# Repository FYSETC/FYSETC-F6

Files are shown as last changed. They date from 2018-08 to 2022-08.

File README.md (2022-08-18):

## Product Introduction

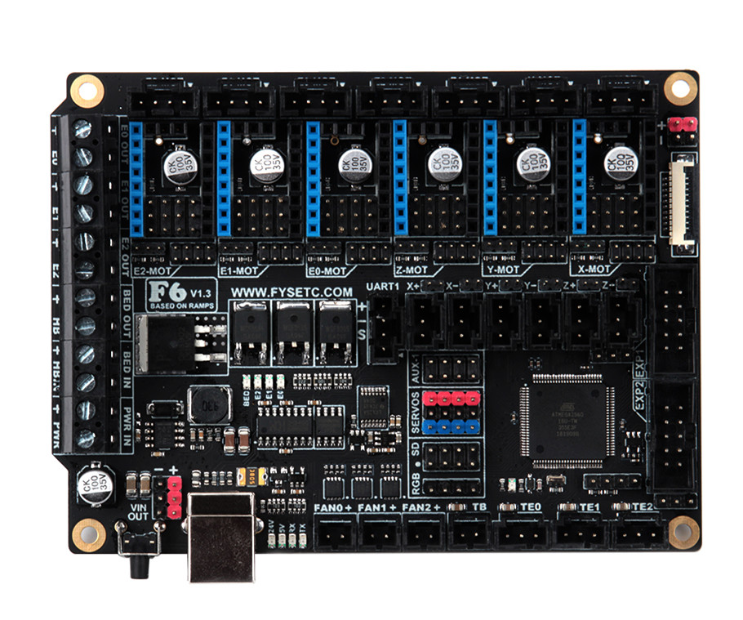
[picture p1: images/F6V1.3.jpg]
F6V1.3


The FYSETC F6 board is a feature rich all-in-one electronics solution for 3D printer and other CNC devices.  It provides six drivers slots and supports Pololu pin compatible stepper drivers, especially the TMC drivers modules. There is no need for flying wires when using TMC2100, TMC2130 and TMC2208. and SPI,Usart and ther pin configer functions are available.

## Features

- Compact size: 117mm x 87mm
- fully integrated all in one solution:
  - Arduino 2560-R3 compatible (works with Sprinter, Repetier-Firmware, Marlin out of the box)
  - CH340 for high speed USB serial connection 
- UNIVERSAL POWER:
  - can be used with 9V-28V for motors / heated bed
  - integrated high precision power regulators (DC/DC):  5V 3A Max 
  - power input auto selector for ATmega/logic (stand alone or power from USB)
- Easy DISPLAY + SD-CARD connector:
  - RepRapDiscount SmartController compatible pin header on board
  - **10P FPC for Serial Touch display**
  - 2X4 PinHeader Out for SD Card moudle 
- **Up to 6 motor drivers with easy micro-steps setup and Supports TMC driver without flying wire**
- 10x PWM capable power mosfet outputs (1 for HotBed, 3 for Heat-End, 3 for fans, 3 for RGB LED strip) 
- The Hot-Bed is designed as a separate power input for maximum current
- All unused pins are led out by pin headers
- <font color=#0099ff size=3 face="~~On Board External 2Mb SPI Flash~~">~~On Board External 2Mb SPI Flash~~</font> 
- PCB：
  - 4 layer
  - 2OZ copper inner layers，1OZ out layers
  - High quality, High temperature FR4-TG130 PCB
  - Gold ENIG finishing

## Application

- 3D printer 
- CNC Device
- Other similar machines

## Hardware Reasources

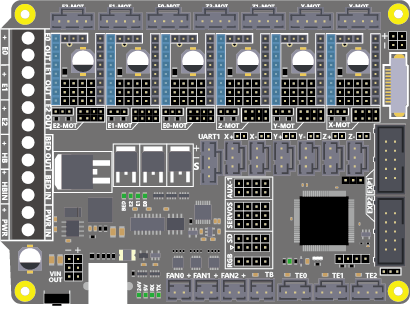
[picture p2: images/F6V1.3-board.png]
F6V1.3-board


| Board Name | F6 |
| --- | --- |
| License | GPL V2.0 |
| Latest Version | V1.3 |
| Extruders | 3 |
| Fixed Fans | 5 Max |
| Controlled Fans | 3 Max |
| Heaters | 3 Max |
| Endstops | 6 Max |
| Temp sens | 4 Max |
| SPI | 1 |
| I2C | 1 |
| ISP | 1 |
| Serial port chip | CH340 |
| CPU | Atmega2560 |
| CPU Speed ( MHz ) | 16 Mhz |
| Stepper driver | 6 Max |
| Stepper driver  Type | All StepStick compatible modules |
| Input | Main PWR：12-24V 10A Max；BED IN：12-24V 15A Max |
| Output | BED OUT：15A Max ；Heater Out：5A Max |

## Jumper for different drivers

In order to support as many different drivers as possible, F6 sets a lot of jumper positions. Different drive modules require different jumpers. The following is a detailed description:

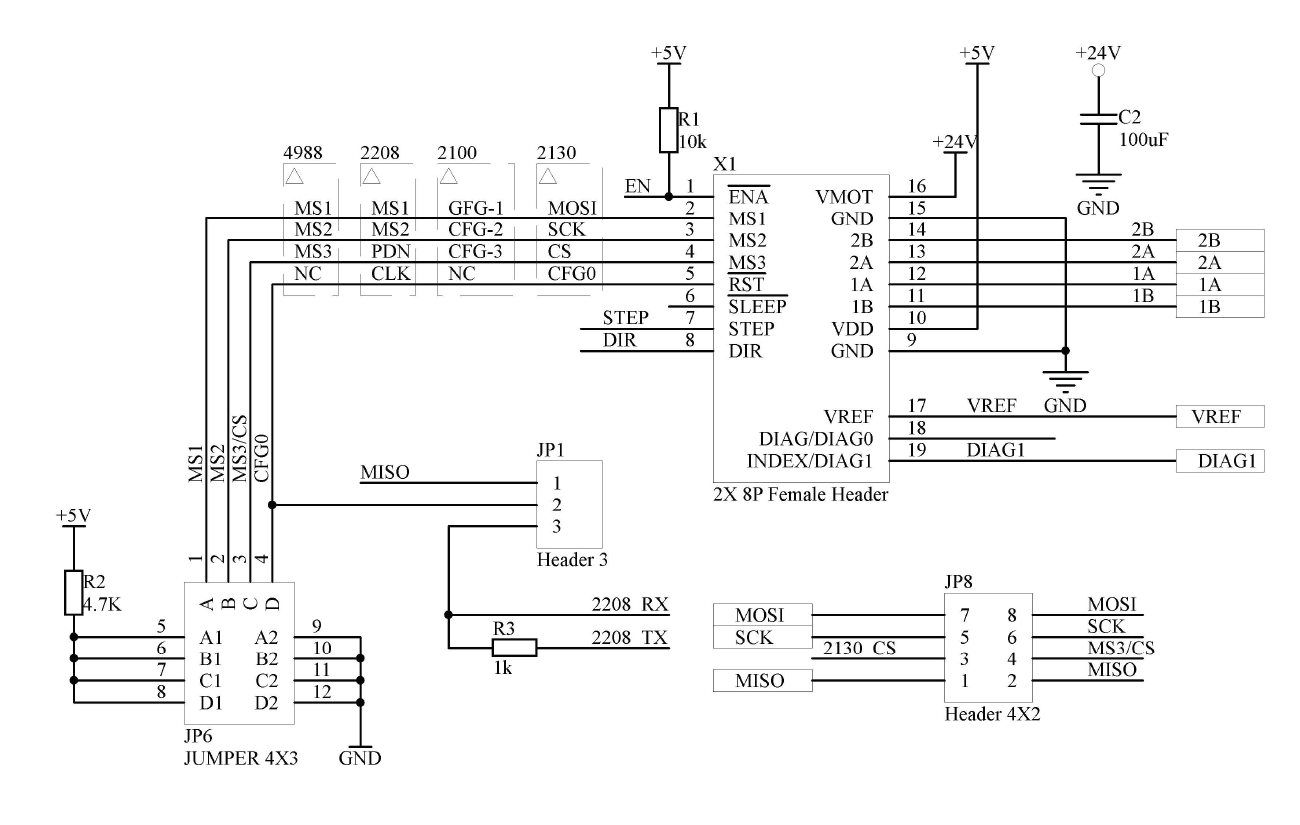
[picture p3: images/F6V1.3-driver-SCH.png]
F6V1.3-driver-SCH


As shown in the schematic diagram above, there are three sets of jumpers in the drive section: JP1, JP6, and JP8. The different driver correspondences are shown in the following table:

| Divers Class | Used jumpers |
|:---:|:---:|
| A4988/DRV8825/THB6128/LV8729 | JP6（only ABC ways） |
| TMC2100 | JP6（only AB ways） |
| TMC2208 | JP1（Short 2&3）&  JP6 |
| TMC2130 | JP1（Short 1&2）&  JP8（Short All） |

#### 1- A4988 and similar series

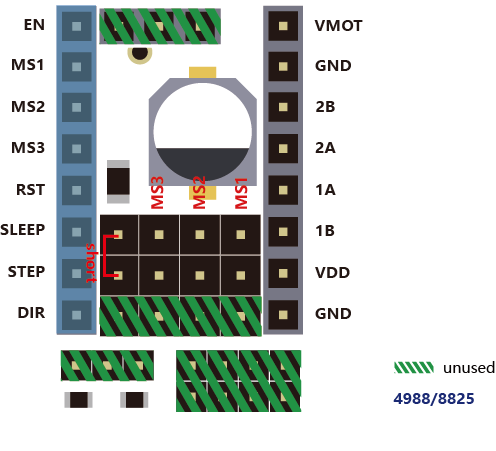
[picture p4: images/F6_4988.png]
F6_4988


If you use the normal A4988 series module, you only need to set the jumper according to the position shown in the figure above, and you should not insert any jumpers in the shaded green part.

#### 2-TMC2100

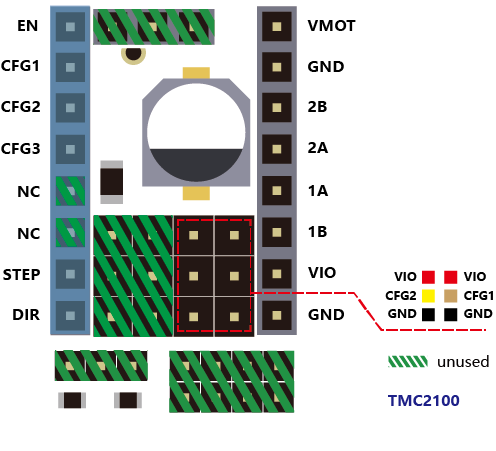
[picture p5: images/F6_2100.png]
F6_2100
 

If you use the TMC2100 module and want to change its microsteps and mode settings, first you must ensure that the CFG1 and CFG2 of the 2100 module are connected by a pin next to it. (For the FYSETC version, you can only perform the welding configuration on the board. The default CFG1 And CFG2 is not connected to the pin header, and the connected version will be sold later)

#### 3-TMC2208

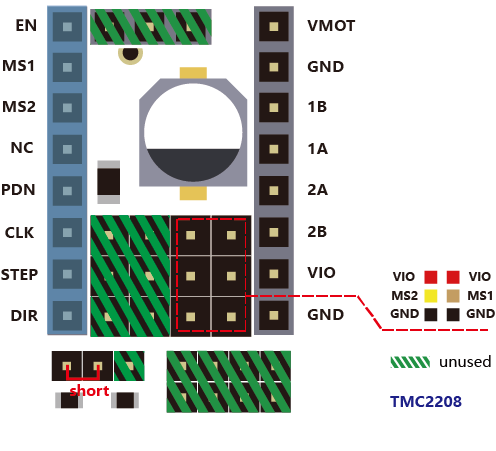
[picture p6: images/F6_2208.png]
F6_2208


If you use the TMC2208, there are two modes to choose . FYSETC's 2208 is factory defaulted to standalone mode. At this mode, you can only set the microsteps by MS1 and MS2.
If you want to config more , you need to enable PDN. First, You must make the jumper next to the PDN pin closed, and second, make sure that the 2 and 3 pin of the JP1 jumper next to the drive position on F6 board is connected , and then, you can make the configuration of the 2208 with marlin (SoftwareSerial).

#### 4-TMC2130

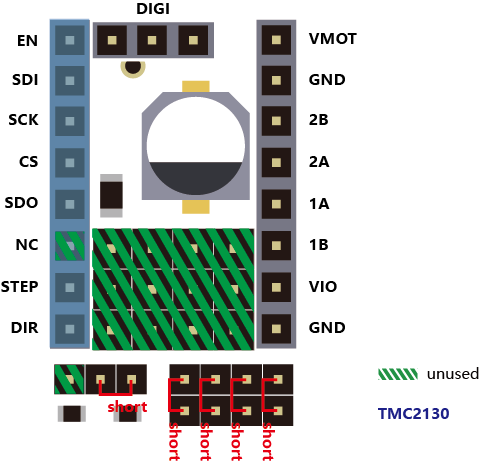
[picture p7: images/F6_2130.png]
F6_2130


If you use the TMC2130, you should use the SPI mode. FYSETC has a version specifically for F6. The jumper settings on the motherboard are as shown above, and the shaded green part is not used. If you want to use the sensorless endstop function of the 2130, you also need to connect the jumper next to the limit switch socket. The corresponding position of each switch is: X- = X, X+ = E2, Y- = Y, Y+ = E1, Z- = Z, Z+ = E0, then configure the firmware, you can use all the features of the 2130.

## Pin Definition



## Firmware Guide

The firmware is in the ```Firmware``` folder.

#### Step1: USB Driver

F6 used a cheap but stable chip for USB to seriel ，CH340，The Driver is here：[https://github.com/FYSETC/CH340-Driver](https://github.com/FYSETC/CH340-Driver)

#### Step2: FYSETC Arduino Plugin

* Instead of manually installing the FYSETC addon's you can now install them from the Arduino Board Manager. From the Arduino File menu select Preferences. 

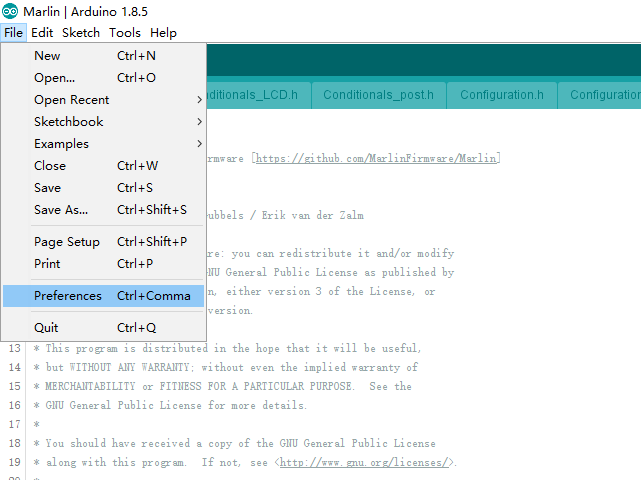
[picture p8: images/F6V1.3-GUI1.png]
F6V1.3-GUI1


* Add the following URL to "Additional Board Manager URLs" section.
  ```https://raw.githubusercontent.com/FYSETC/ArduinoAddons/master/package_fysetc_index.json```

![F6V1.3-GUI2](images/F6V1.3-GUI2.png)

* Open the “Boards Manager”.

![F6V1.3-GUI3](images/F6V1.3-GUI3.png)

* Search the "FYSETC_F6"

![F6V1.3-GUI4](images/F6V1.3-GUI4.png)

If you want to use F6 V1.4 , you need to update the addon to 1.4.0

![image-20200112164039226](images/F6V1.4.png)

* And then install it.

![F6V1.3-GUI5](images/F6V1.3-GUI5.png)

#### Step3: Configure firmware

* Change the board type configuration in configuration.h 
  
  F6 V1.3: BOARD_FYSETC_F6_13
  
  F6 V1.4: BOARD_FYSETC_F6_14

![F6V1.3-GUI9](images/F6V1.3-GUI9.png)

#### Step4: Install TMC2130/TMC2208 library

If you want to use the 1.1.x version frimware ,and you want use TMC2130/TMC2208 driver , you need to install TMC2130/TMC2208 library.

Click "Manage Libraries" .

![1574739668740](images/F6-ManageLib.png)

Type "TMC" and Enter to search for TMC2130/TMC2208 library by teemuatlut. Click 'Install' button to install the library.

![1574739717005](images/F6-TMCLib-Search.png)

#### Step5: Install TMC library

If you want to use the 2.0.x version frimware , and you want to use TMC stepper drivers , you need to install TMCStepper library.

Click "Manage Libraries" .

![1574739668740](images/F6-ManageLib.png)

Type "TMCStepper" and Enter to search for TMCStepper library by teemuatlut. Click 'Install' button to install the library if you did not install it.

![TMCStepperDriver](images/F6-TMCStepperDriver.png)

#### Step6: Connect the USB cable

Connect a USB cable between your computer and the machine.Then click Tools->Port and select the COM port.

![F6V1.4-GUI6](images/F6-ConnectUSB.png)

#### Step7: Upload

Click the arrow button to upload.

![F6V1.4-GUI7](images/F6V1.4-GUI7.png)

## Platformio

How to build `F6 v1.4`

Replace the file  `C:\Users\*username*\.platformio\packages\framework-arduino-avr\variants\fysetcf6\pins_arduino.h` with the one in the repository.

## Attachments

- [Schematic files](https://github.com/FYSETC/F6/blob/master/F6_V13.pdf)
- [PCB files](https://github.com/FYSETC/F6/blob/master/GERBER_F6_13.zip)

## Shop

- [FYSETC-F6V1.3](https://www.aliexpress.com/item/FYSETC-F6-Board-ALL-in-one-Electronics-Solution-For-3D-Printer-CNC-Devices-Up-to-6/32911155606.html)
- [TMC2100/2130/2208](https://www.aliexpress.com/store/product/5PCS-TMC2100-V1-3-TMC2130-TMC2208-Stepper-Motor-StepStick-Mute-Driver-Silent-Excellent-Stability-Protection-For/3480083_3284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)

## Tech Support

Please submit any technical issue into our [forum](http://forum.fysetc.com/)

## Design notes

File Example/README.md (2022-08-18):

# Example

## VORON

`fysetc-f6-for-voron.stl` for you to mount F6 board to VORON machine. And `fysetc-f6-for-voron-Trident-printer.cfg` is Klipper example cfg file for VORON Trident machine.

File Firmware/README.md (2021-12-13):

# Firmware

## 1. Marlin

This firmware is base on the upstream [Marlin 2.0.x](https://github.com/MarlinFirmware/Marlin/tree/2.0.x). And it is just for a sample, all PRs for F6 board are in the latest upstream branch, you can download the latest upstream branch and compare the ```configuration.h``` and  ```configuration_adv.h``` file to setup firmware for F6.

### 4.3'' Touch SCREEN

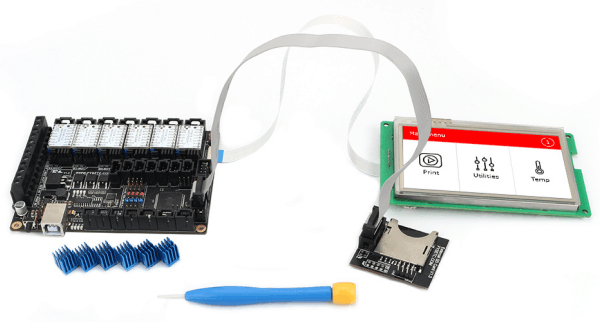
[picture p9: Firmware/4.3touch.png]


If you use FYSETC 4.3'' touch screen, please follow the [README](https://github.com/FYSETC/FYSTLCD-2.0) here. There are pre-build firmwares for you to test your screen named ```F6-4.3Touch.hex```.

## 2. Klipper

We provide you an example `printer.cfg` file for VORON Trident machine in `Klipper` folder.

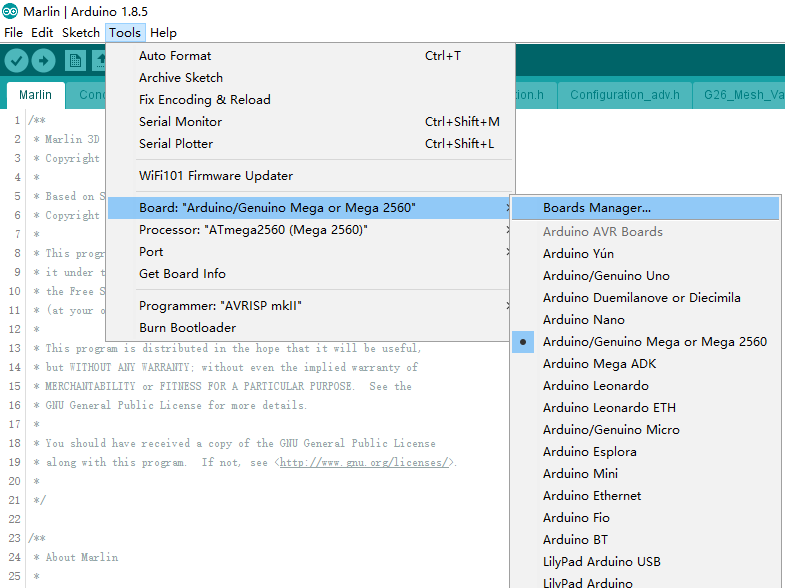
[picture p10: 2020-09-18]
images/F6V1.3-GUI3.png

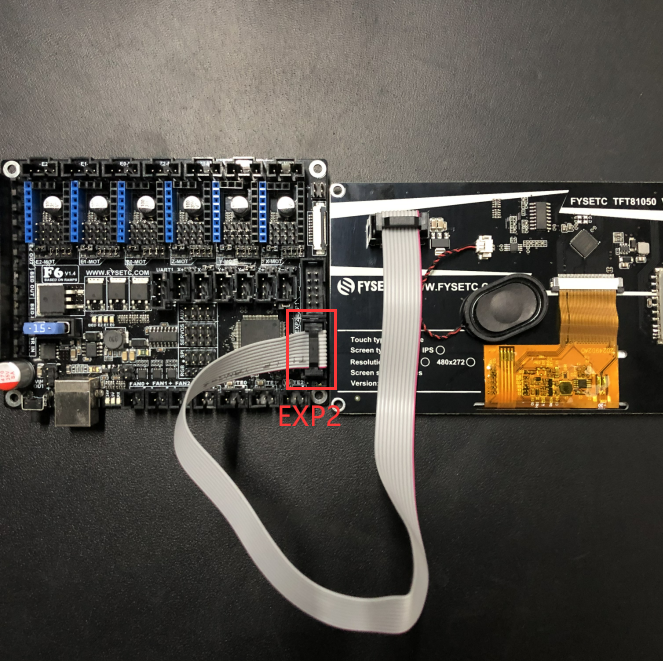
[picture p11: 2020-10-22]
images/F6-FTDI.png

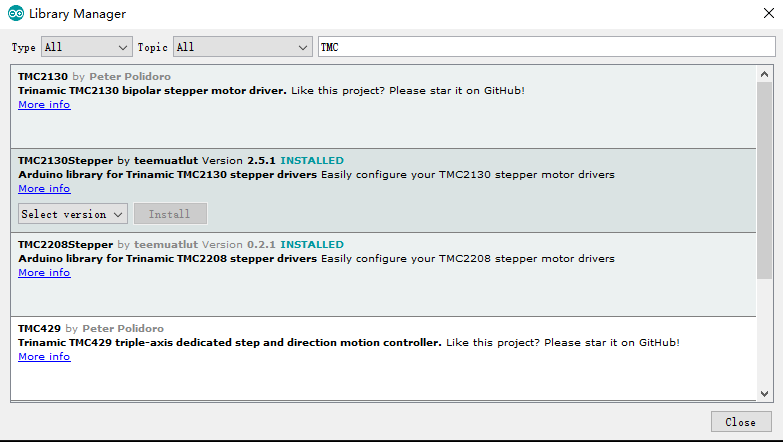
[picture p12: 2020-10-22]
images/F6-TMCLib-Search.png

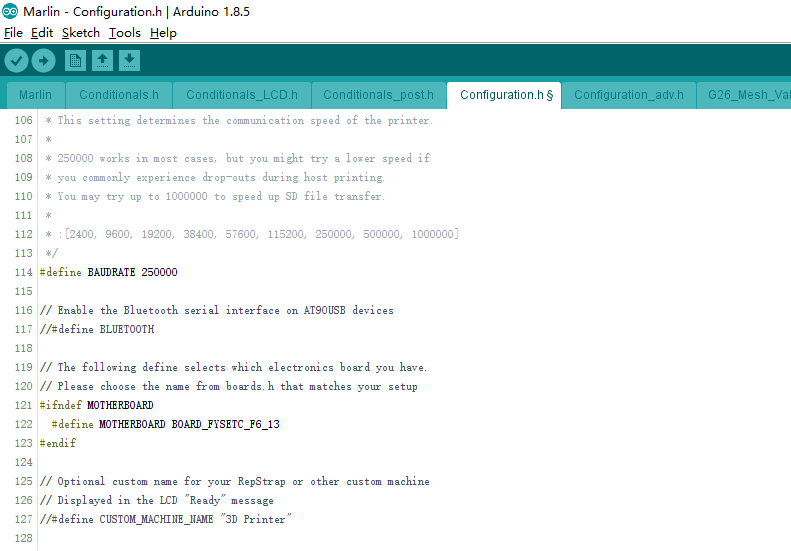
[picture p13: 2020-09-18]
images/F6V1.3-GUI9.png

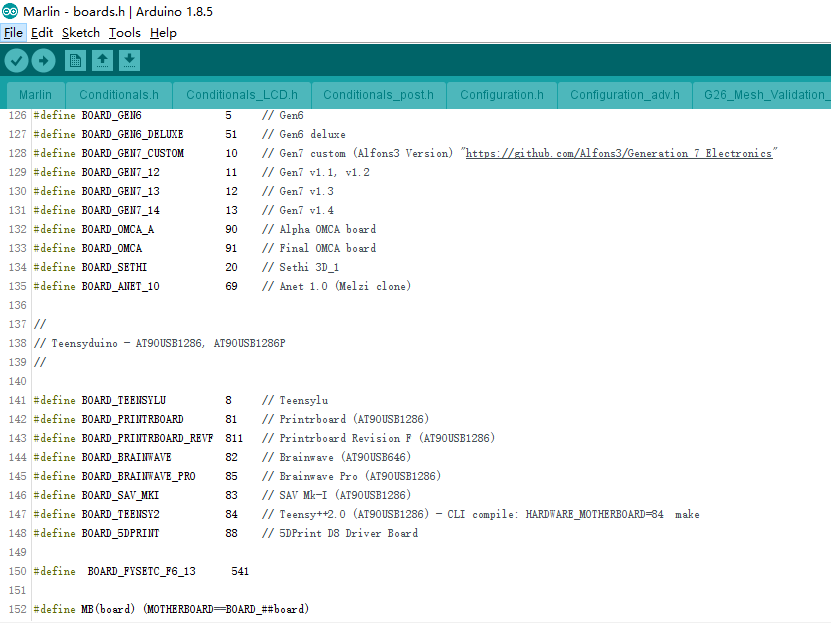
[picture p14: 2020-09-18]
images/F6V1.3-GUI7.png

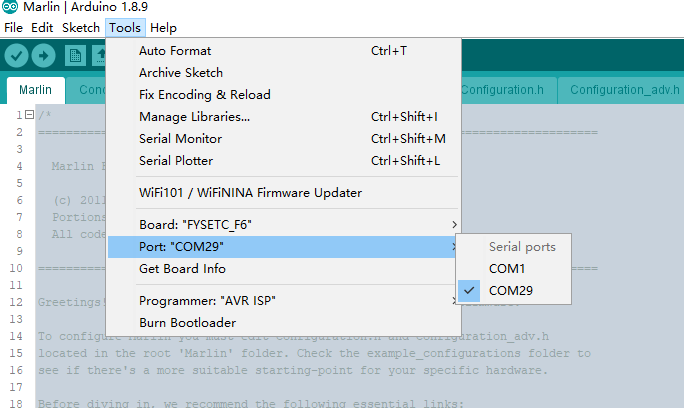
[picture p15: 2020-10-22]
images/F6-ConnectUSB.png

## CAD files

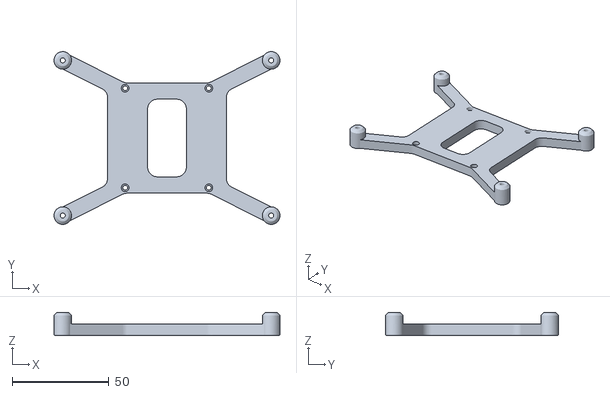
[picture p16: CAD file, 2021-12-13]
Example/fysetc-f6-for-voron.stl
116.5 x 89.1 x 11.9

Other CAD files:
Hardware/V1.3/F6 V1.3 2D.DWG

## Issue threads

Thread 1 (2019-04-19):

Fysetc F6 connectors

Paulbsh, 2019-04-19:
I'm still not able to log into the forum, that's why I'm asking here:
What connectors does the F6 use?
Looks like standard 2.54 pitch headers, so DuPont would work.
But I want to use the correct connectors.

Thanks

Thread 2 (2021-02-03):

USB backfeeding through Q5

TylorKing, 2021-02-03:
The USB port is back feeded with 3.7 V.
This is propably caused by the body diode of Q5 (FDN340P).
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
A fix would be replacing the FDN340P with a back to back mosfet (available in a single package).

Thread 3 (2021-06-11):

FYSETC F6 V1.3 TMC CONNECTION ERROR

Miran81, 2021-06-11:
Hi,
I'm using marlin 2.0 and i have  X is tmc 2130 Y and Z axis step motor drivers TMC2209 and i get tmc connection error. Need help. This my pins;
#define X_SERIAL_RX_PIN       71
 #define X_SERIAL_TX_PIN       72

 #define Y_SERIAL_RX_PIN       73
 #define Y_SERIAL_TX_PIN       75

 #define Z_SERIAL_RX_PIN       78
 #define Z_SERIAL_TX_PIN       79

 #define E0_SERIAL_RX_PIN      76
 #define E0_SERIAL_TX_PIN      77

 #define E1_SERIAL_RX_PIN      80
 #define E1_SERIAL_TX_PIN      81

 #define E2_SERIAL_RX_PIN      22
 #define E2_SERIAL_TX_PIN      82

#endif
*****************************************************************************************
SENT: M122
RECEIVED: Testing X connection... Error: All LOW
RECEIVED: Testing Y connection... Error: All LOW
RECEIVED: Testing Z connection... Error: All LOW
RECEIVED: ok

Miran81, 2021-06-13:
When i sd card insterted, sd card region sparked. Please help

Miran81, 2021-06-14:
ANY HELP

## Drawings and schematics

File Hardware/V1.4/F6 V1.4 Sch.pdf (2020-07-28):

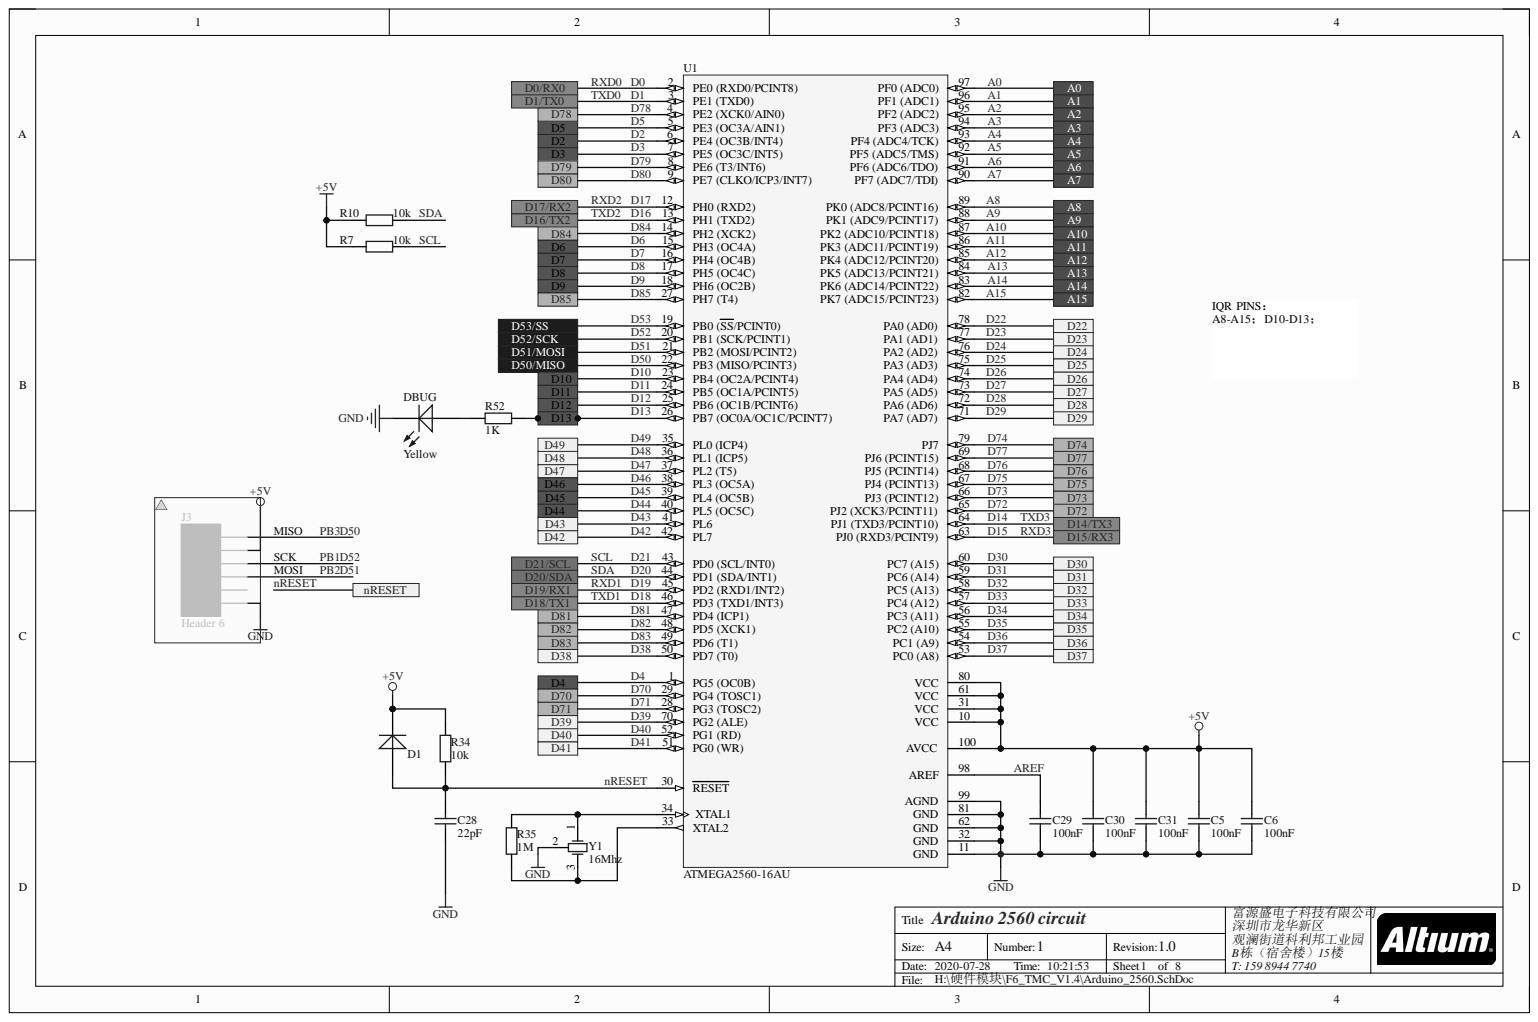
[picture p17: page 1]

D 1 / T X 0 | | | A 1
D 7 8 | | | A 2

D 7 8 | 9 5 A 2
D 5 | 9 4 A 3
D 2 6 | 9 3 A 4
D 3 7 | 9 2 A 5
D 7 9 8 | 9 1 A 6
D 8 0 9 | 9 0 A 7

D 7 9 | | | A 6
D 8 0 | | | A 7

D 8 4 | | | A 1 0
D 6 | | | A 1 1

D 7 1 6 | 85 PK3 (ADC11/PCINT19) 86 4 PK4 (ADC12/PCINT20) A 1 2

D 8 1 7 | 8 A 1 3
D 9 1 8 | 8 3 A 1 4
D 8 5 2 | 8 2 A 1 5

D 9 | | | A 1 4
D 8 5 | | | A 1 5

D 5 2 2 | | 7 7 D 2 3
D 5 1 2 1 | | 7 6 D 2 4
D 5 0 2 2 | | 7 5 D 2 5
D 1 0 2 3 | | 7 4 D 2 6
D 1 1 2 4 | | 7 3 D 2 7
D 1 2 2 5 | | 7 2 D 2 8
D 1 3 2 6 | | 7 1 D 2 9

D 5 1 /MOSI | | | | D 2 4
D 5 0 /MISO | | | | D 2 5

D 4 8 3 6 | | D 7 7
D 4 7 3 7 | | 6 D 7 6
D 4 6 3 8 | | 6 7 D 7 5
D 4 5 3 9 | | 6 6 D 7 3
D 4 4 4 0 | | 6 5 D 7 2
D 4 3 4 1 | | 6 4 D 1 4 T X D 3

D 4 6 | | | | D 7 5
4 5 | | | | D 7 3

D 8 1 | | D 3 4
D 8 2 | | D 3 5

D 8 3 4 9 | | 5 D 3 6
D 3 8 5 0 | | 5 3 D 3 7

D 7 0 2 9 | 6 1
D 7 1 2 8 | 3 1
D 3 9 7 0 | 1 0
D 4 0 5 | 1 0 0

ARE F

9 9
8 1

3 4
3 3 | 6 2

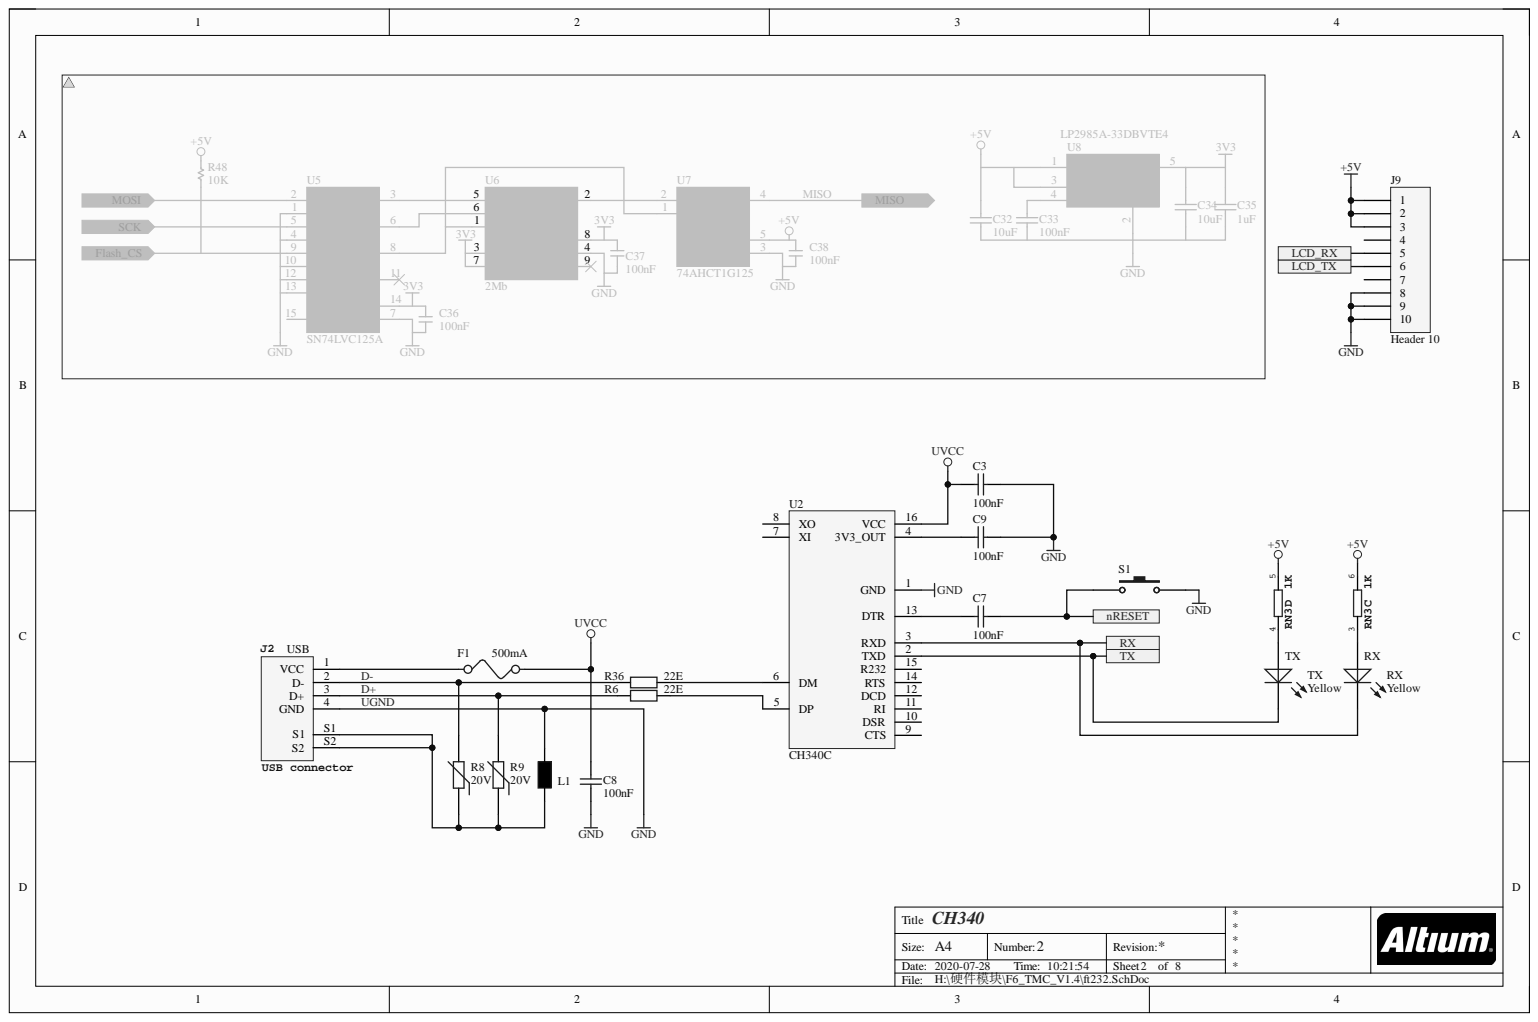
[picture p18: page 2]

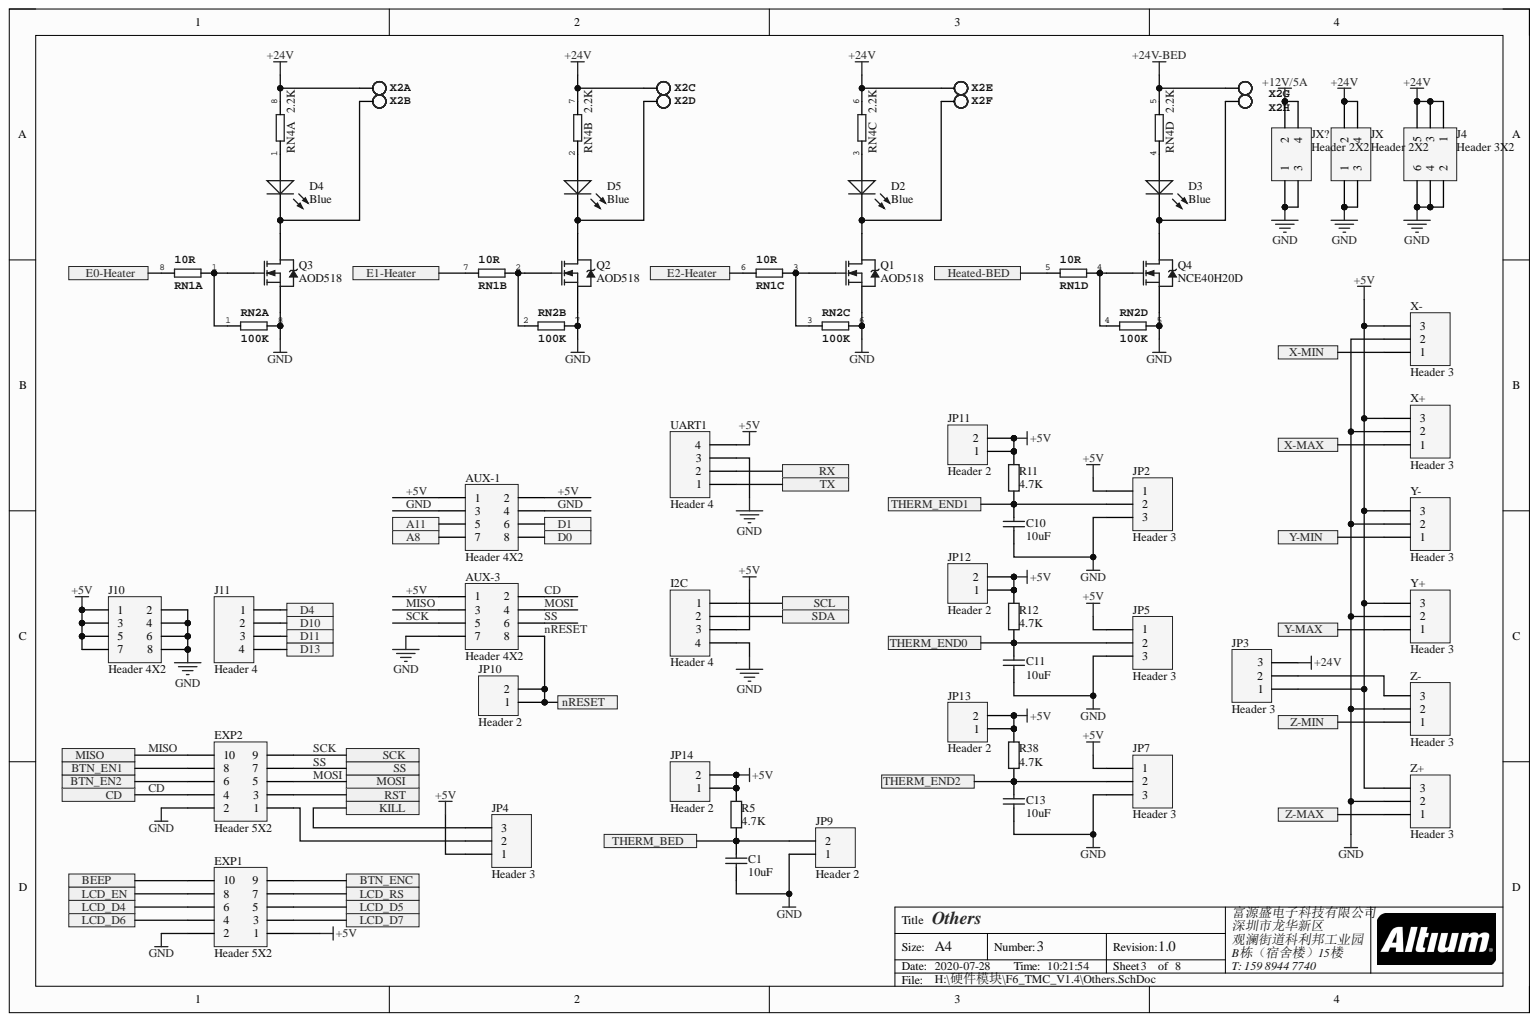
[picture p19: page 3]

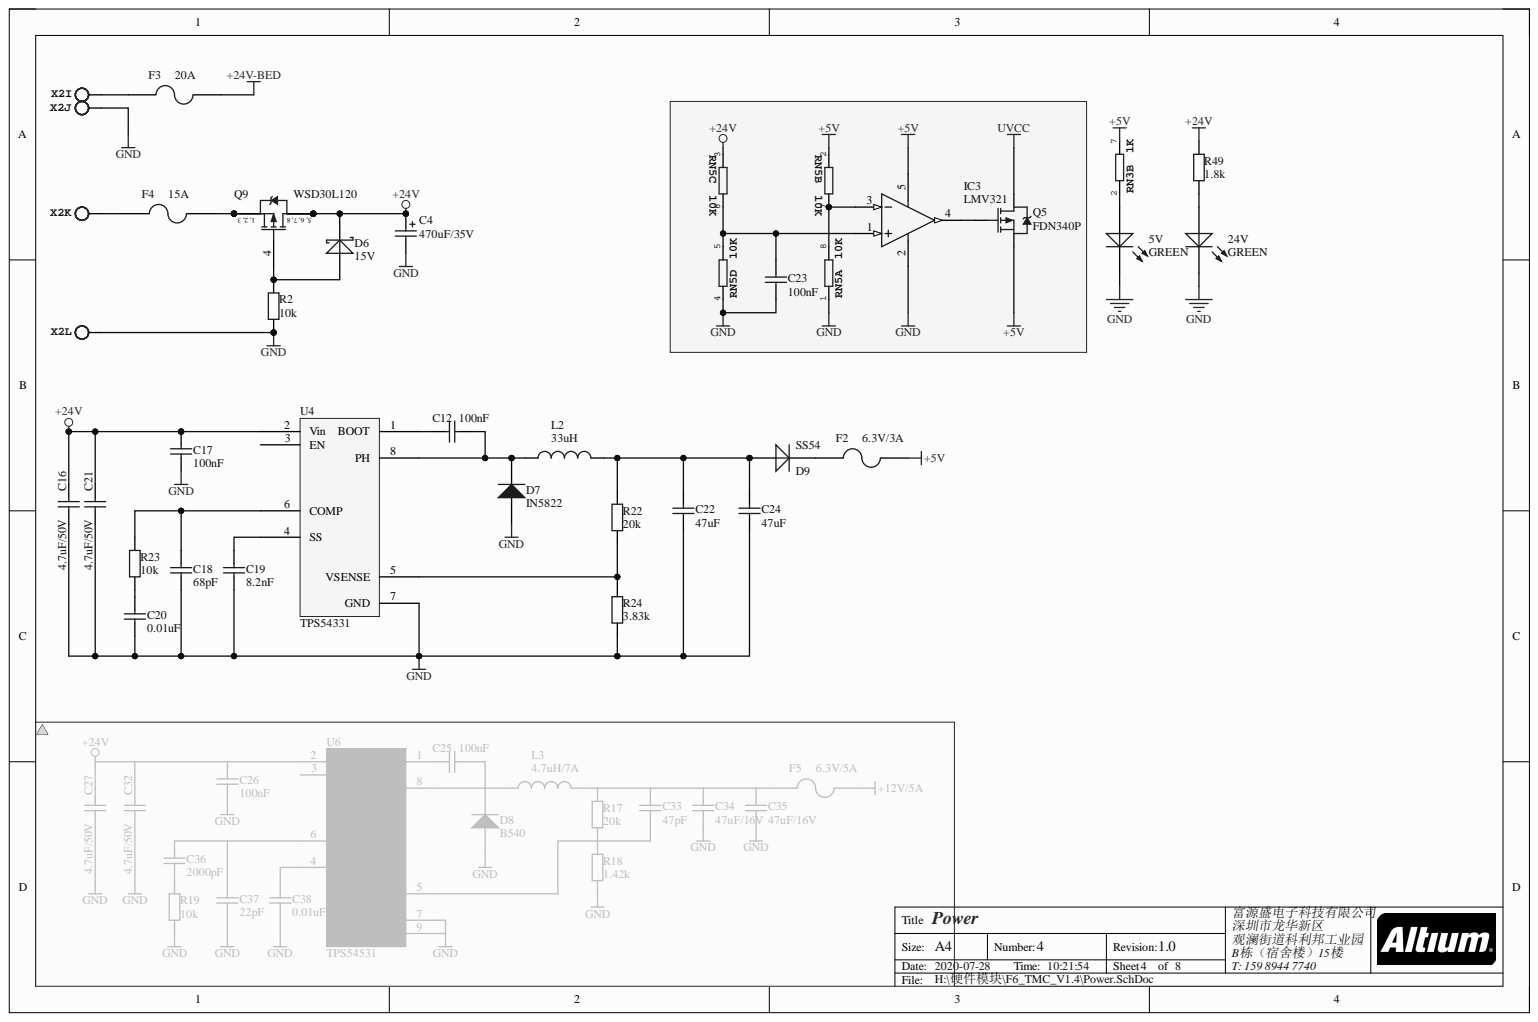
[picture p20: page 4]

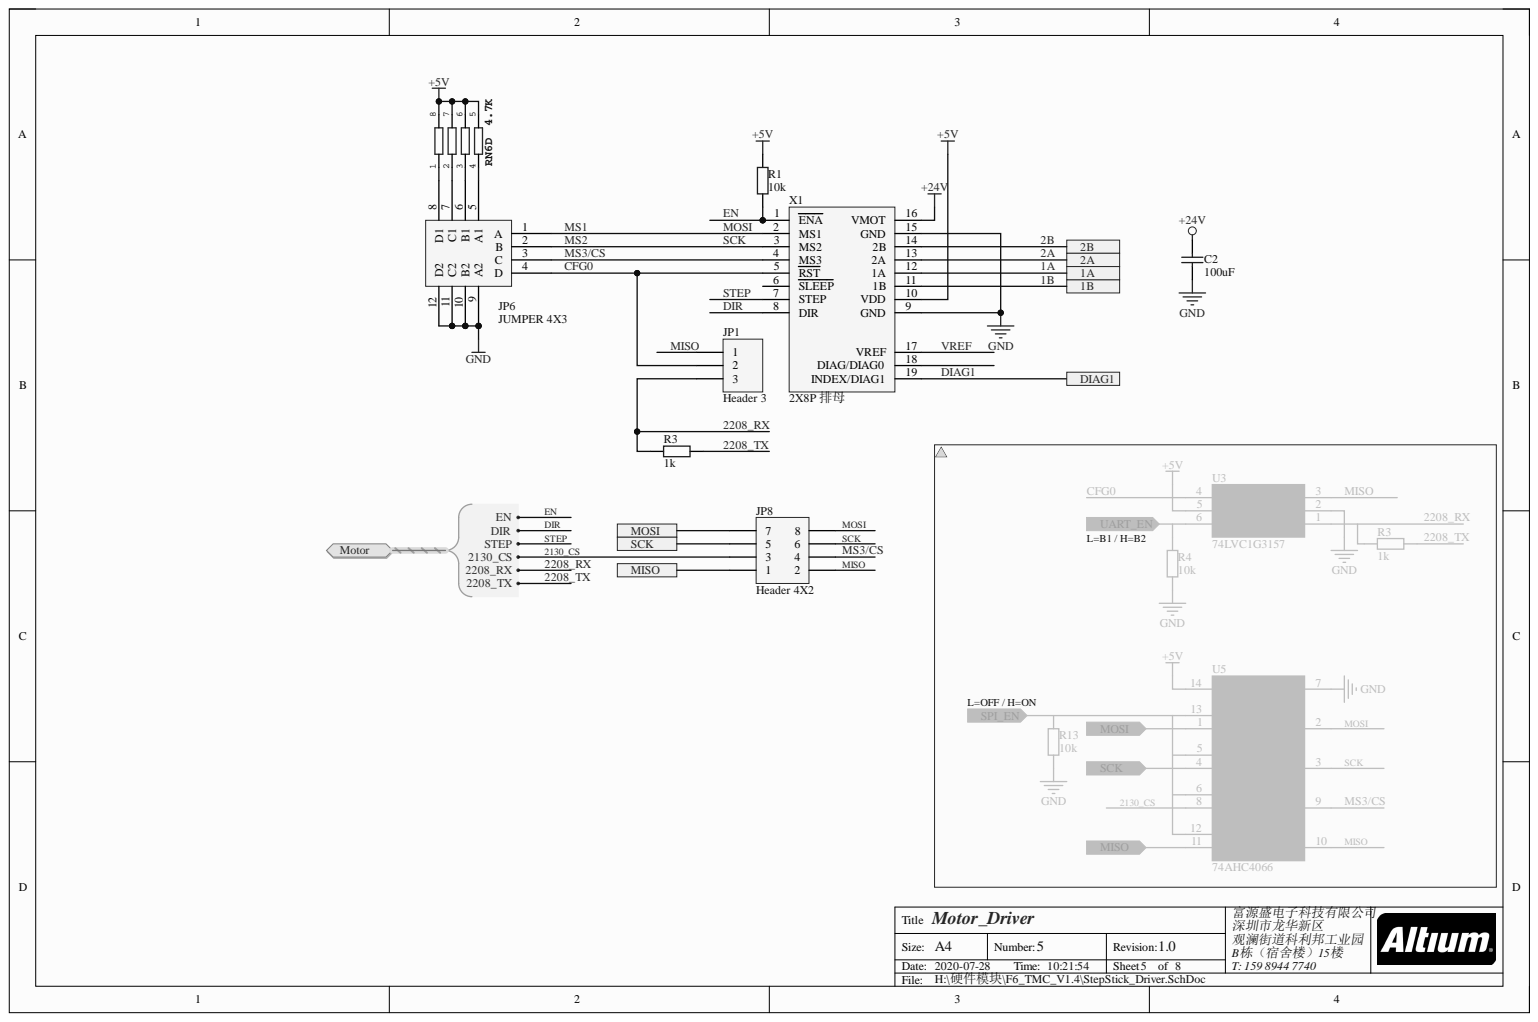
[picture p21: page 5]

2 MS2 SCK 3 | | 1 4
3 MS3 /CS 4 | | 1 3 | | 2 A
4 CFG 0 5 | | 1 2 | | 1 A

MISO | 6 ST E P | 1 1 | | 1 B

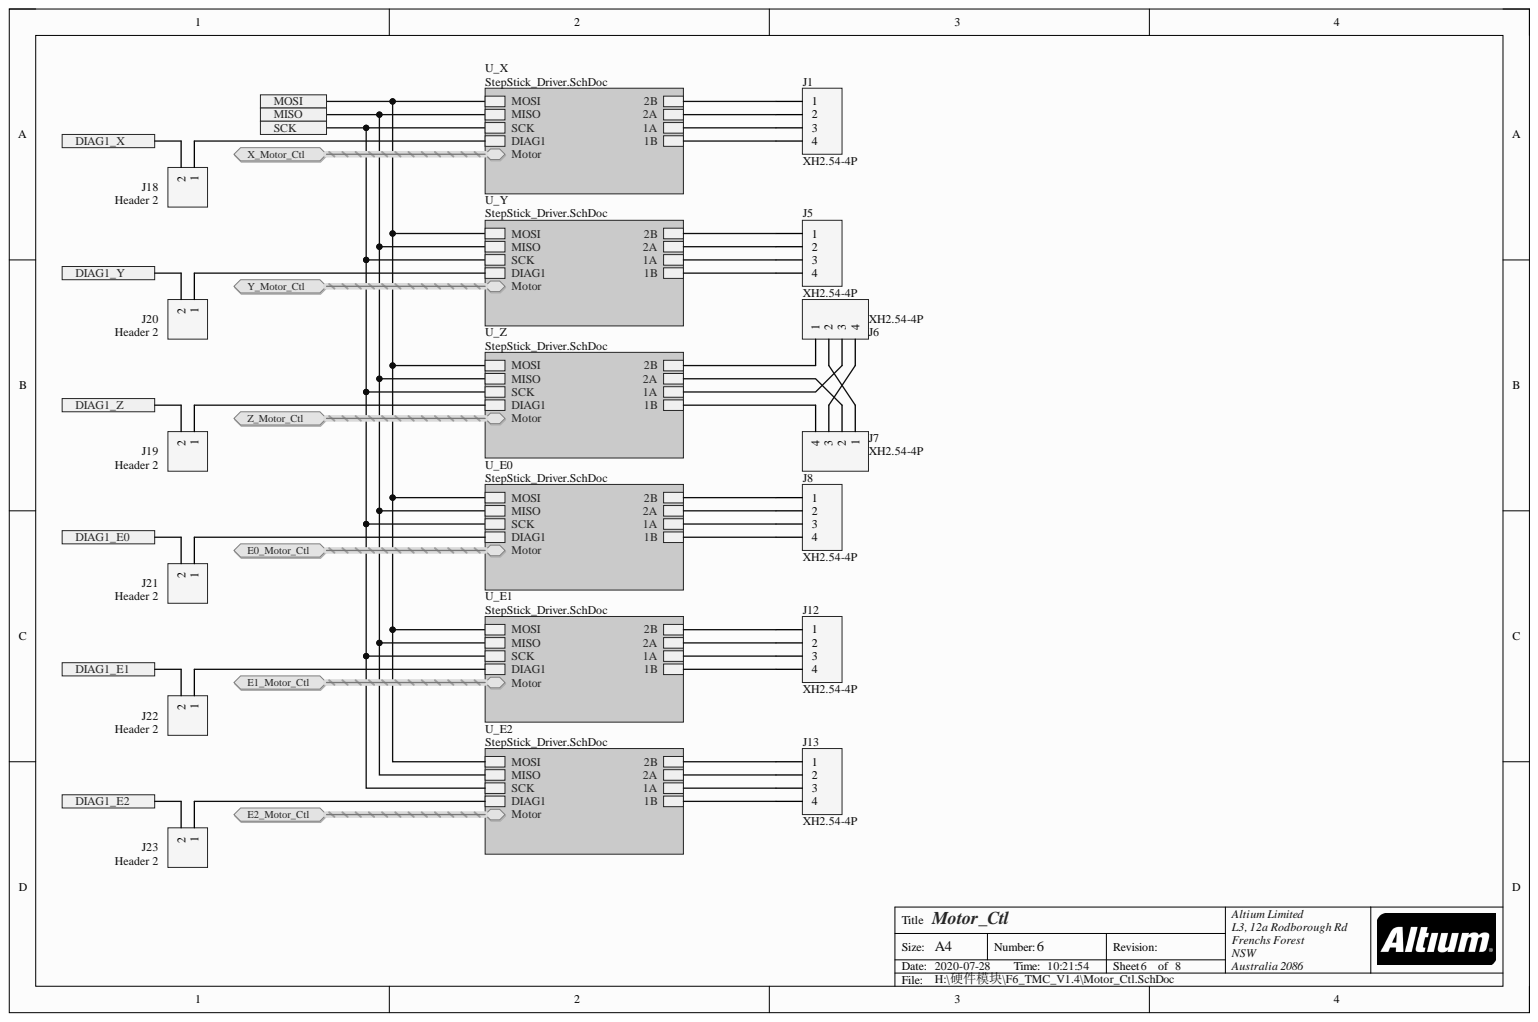
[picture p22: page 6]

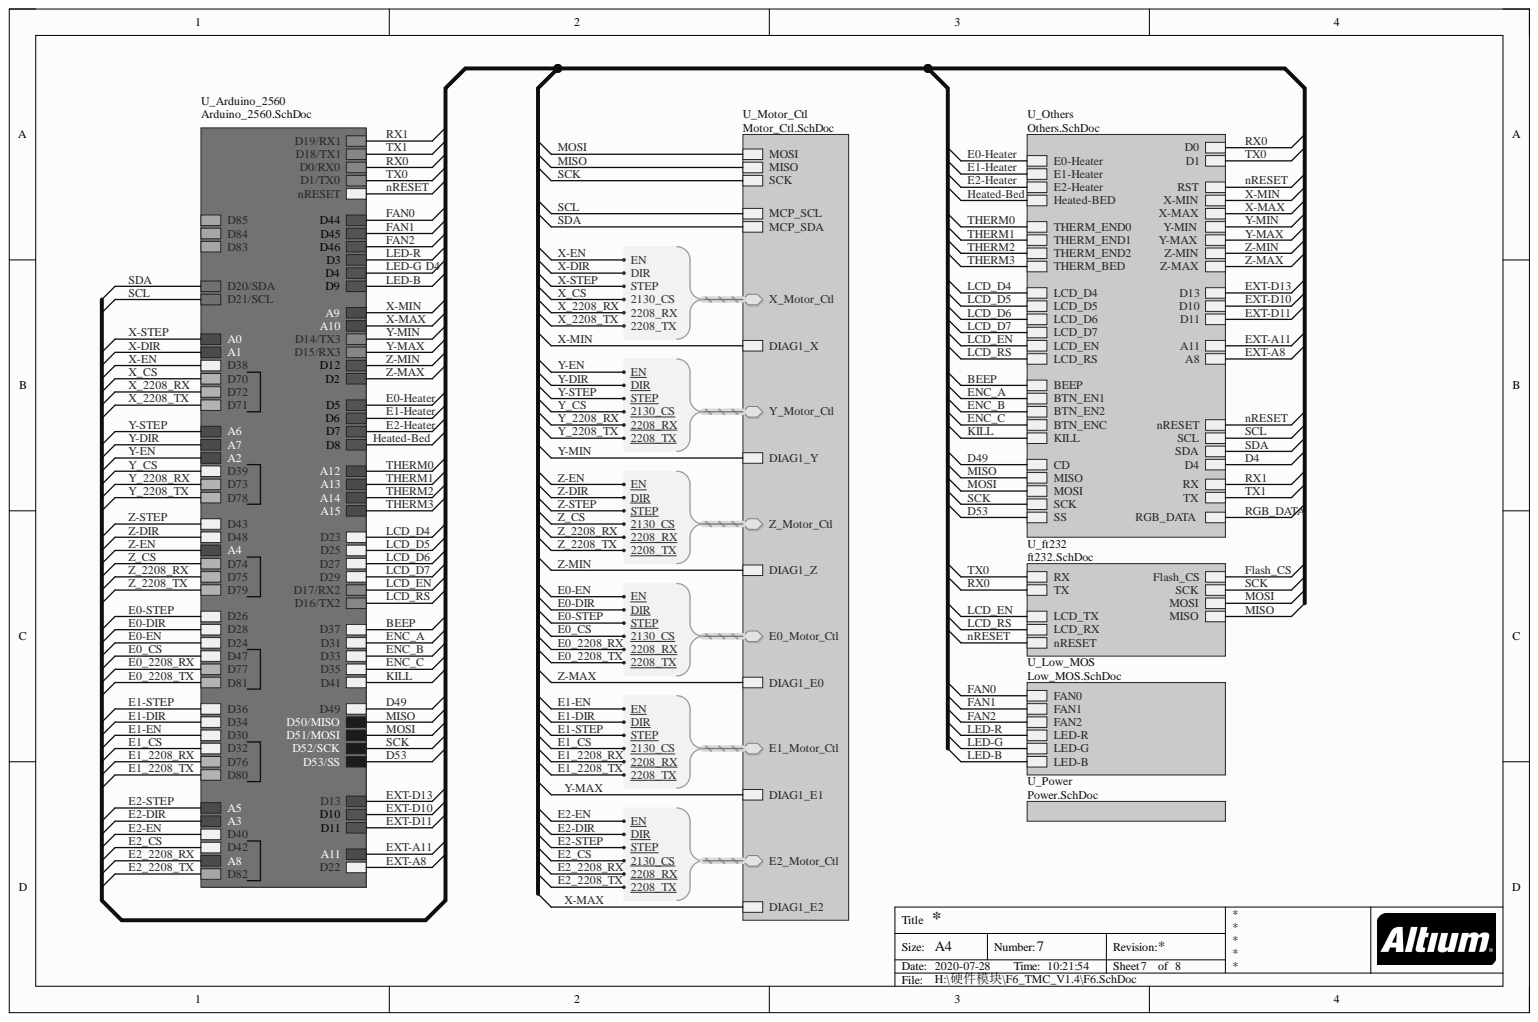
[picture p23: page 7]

hers.Sch
SCK D53 E1-Heater Heated-Bed E0-Heater E2-Heater THERM2 LCD_RS LCD_EN THERM3 ENC_C KILL LCD_D4 LCD_D5 LCD_D6 LCD_D7

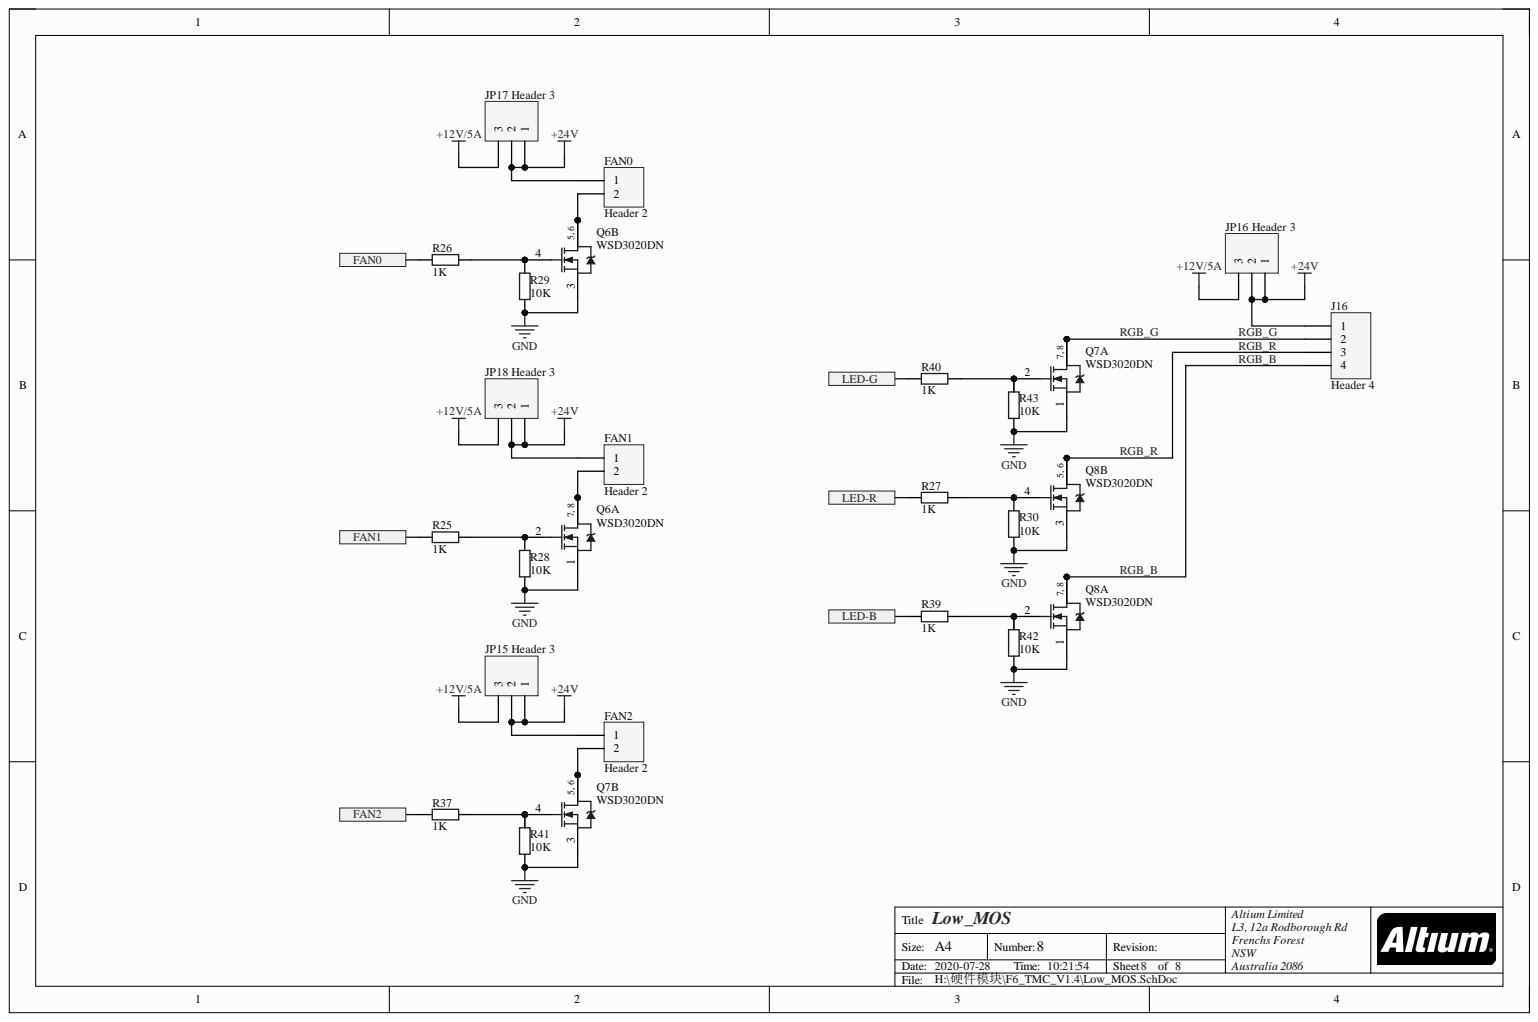
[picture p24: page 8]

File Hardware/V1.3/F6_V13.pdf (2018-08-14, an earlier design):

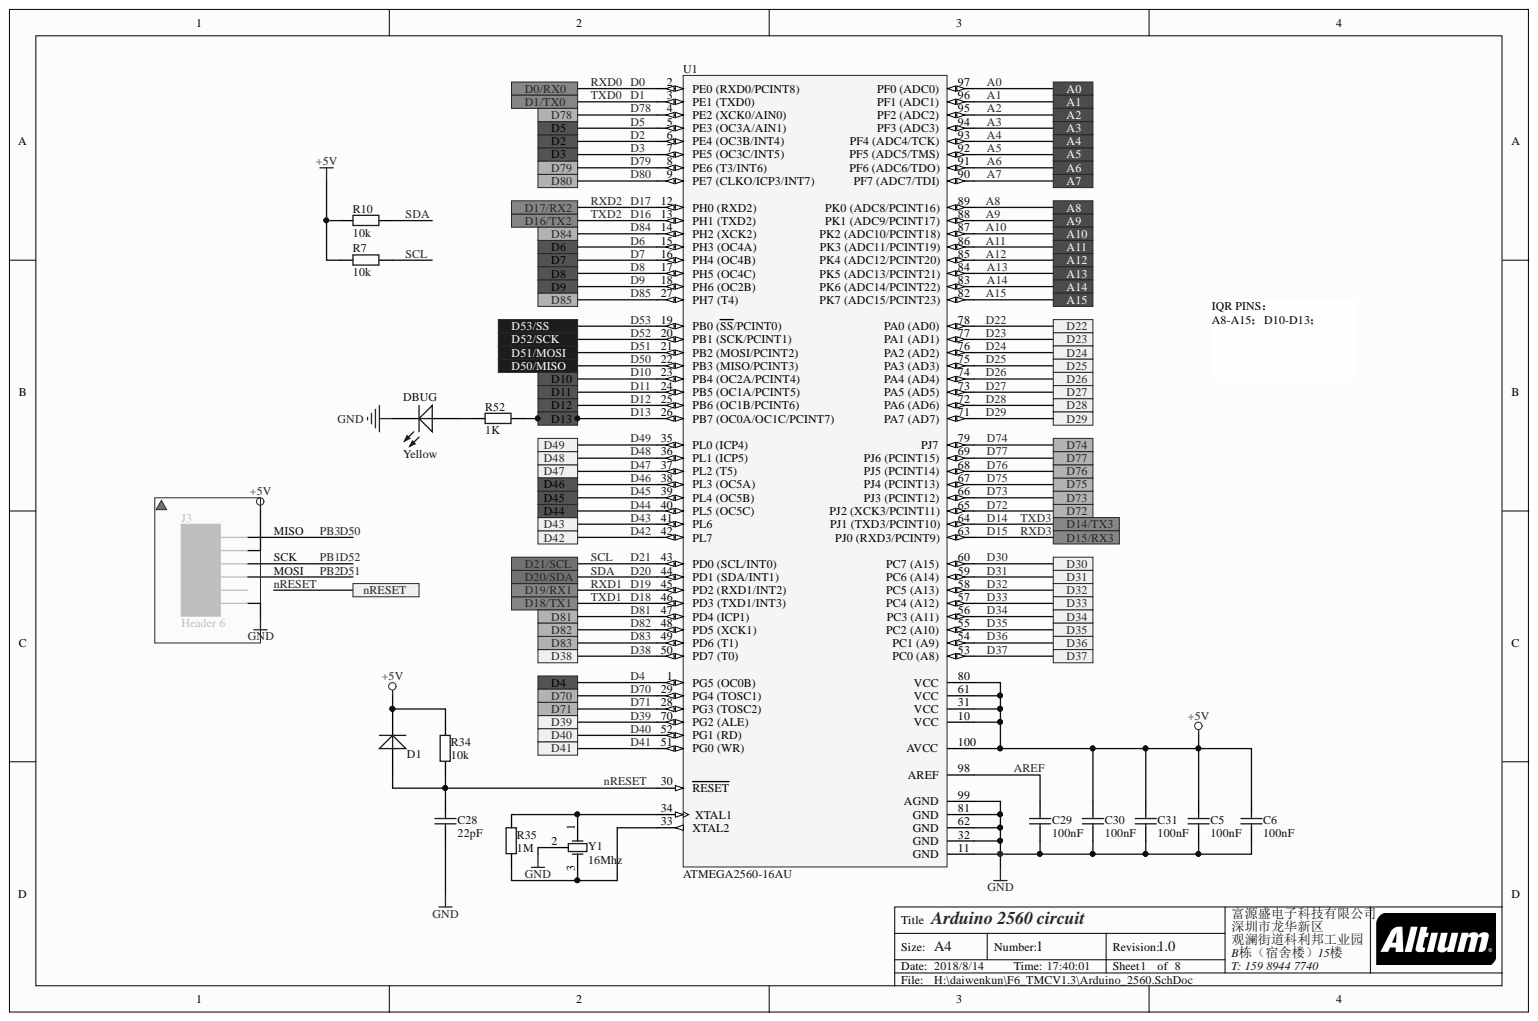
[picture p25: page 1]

D 7 8 | | 9 5 A 2
D 5 | | 9 4 A 3
D 2 6 | | 9 3 A 4
D 3 7 | | 9 2 A 5
D 7 9 8 | | 9 1 A 6
D 8 0 9 | | 9 0 A 7

D 8 4 1 4 | 8 7 A 1 0
D 6 1 5 | A 1 1

D 7 1 6 | 85 PK3 (ADC11/PCINT19) 86 4 PK4 (ADC12/PCINT20) A 1 2

D 8 1 7 | 8 A 1 3
D 9 1 8 | 8 3 A 1 4
D 8 5 2 | 8 2 A 1 5

D 5 2 2 | | 7 7 D 2 3
D 5 1 2 1 | | 7 6 D 2 4
D 5 0 2 2 | | 7 5 D 2 5
D 1 0 2 3 | | 7 4 D 2 6
D 1 1 2 4 | | 7 3 D 2 7
D 1 2 2 5 | | 7 2 D 2 8
D 1 3 2 6 | | 7 1 D 2 9

D 5 1 /MOSI | | | | D 2 4
D 5 0 /MISO | | | | D 2 5

D 4 8 3 6 | | D 7 7
D 4 7 3 7 | | 6 D 7 6
D 4 6 3 8 | | 6 7 D 7 5
D 4 5 3 9 | | 6 6 D 7 3
D 4 4 4 0 | | 6 5 D 7 2
D 4 3 4 1 | | 6 4 D 1 4 T X D 3

D 4 | | | | D 7 5
4 5 | | | | D 7 3

D 8 1 | | D 3 4
D 8 2 | | D 3 5

D 8 3 4 9 | | 5 D 3 6
D 3 8 5 0 | | 5 3 D 3 7

D 7 0 2 9 | 6 1
D 7 1 2 8 | 3 1
D 3 9 7 0 | 1 0
D 4 0 5 | 1 0 0

ARE F

9 9
8 1

3 4
3 3 | 6 2

Arduino 2 5 T i t l e | 富源盛电子科技有限公司 深圳市龙华新区 观澜街道科利邦工业园 B栋（宿舍楼）15楼 T: 1 9 8 4 7

Size: A4 | N umber: | Rev i s i o n : 1.0
Date: / T ime: : | | Sheet f

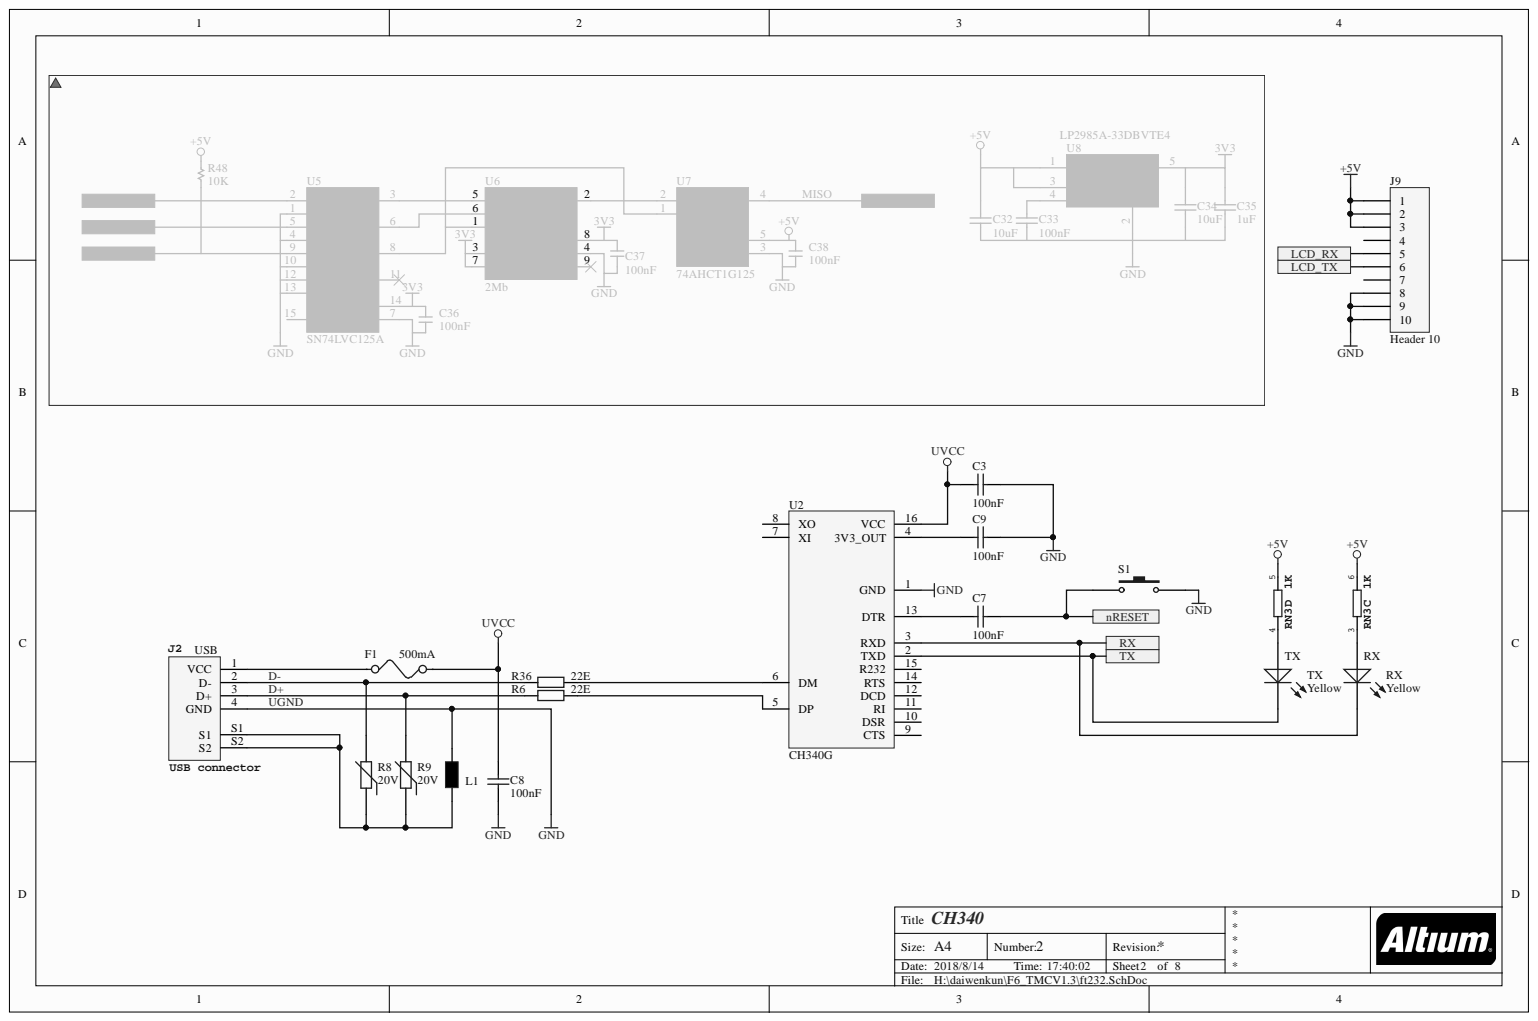
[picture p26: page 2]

Size: A4 | N umber: 2 | Rev i s i o n : *

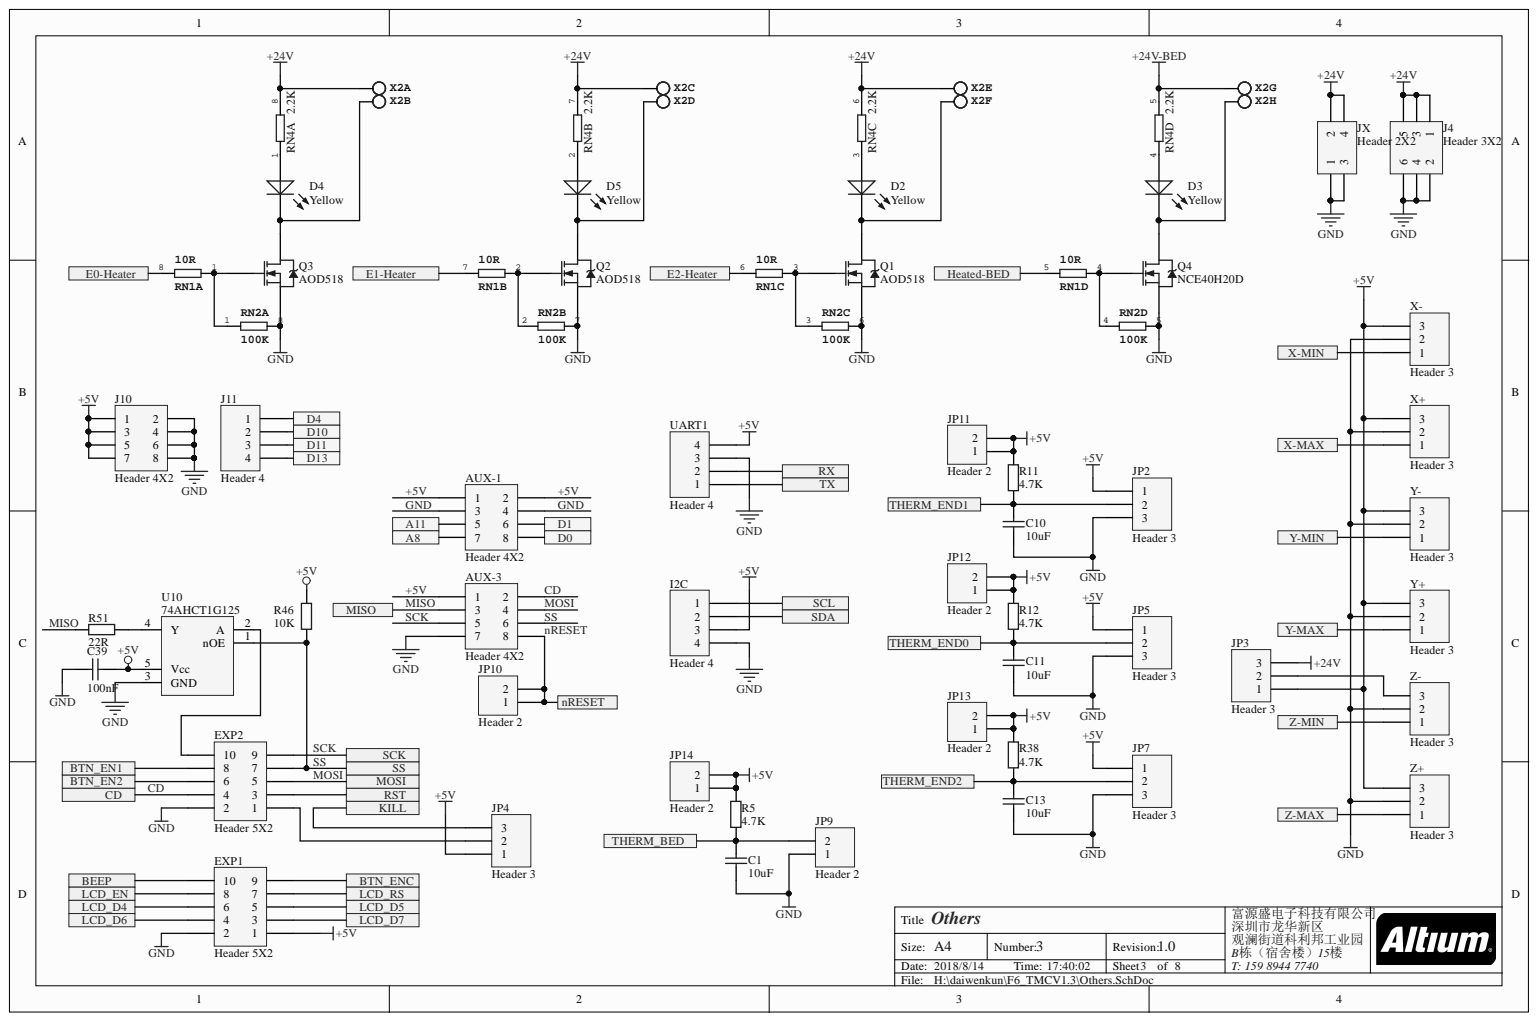
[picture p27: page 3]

LCD_EN | LCD_RS

Others Title | 富源盛电子科技有限公司 深圳市龙华新区 观澜街道科利邦工业园 T: 159 8944 7740

Size: A4 | Number: 3 | Revision: 1.0 | B栋（宿舍楼）15楼 8
2018/8/14 Time: 17:40:02 | | Sheet of

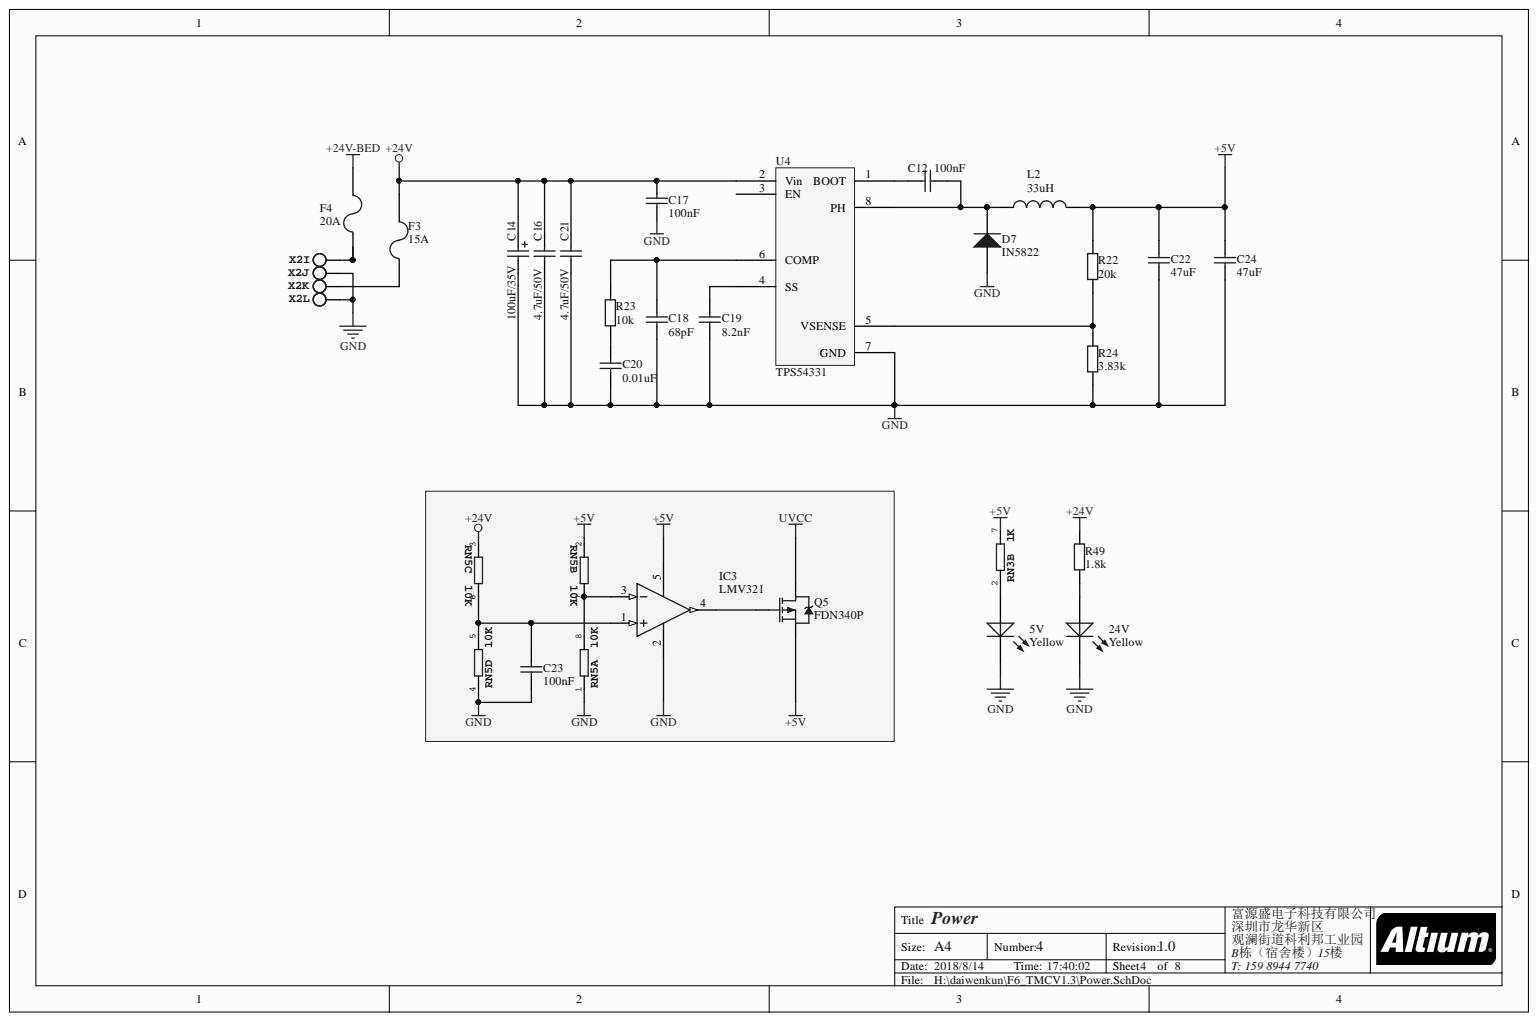
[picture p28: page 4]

Power T i t l e | 富源盛电子科技有限公司 深圳市龙华新区 观澜街道科利邦工业园 B栋（宿舍楼）15楼 T: 1 9 8 4 7

Size: A4 | N umber: 4 | Rev i s i o n : 1.0


Motor_Driver Title | 富源盛电子科技有限公司 深圳市龙华新区 观澜街道科利邦工业园 T: 159 8944 7740

Size: A4 | Number: 5 | Revision: 1.0 | B栋（宿舍楼）15楼 8
2018/8/14 Time: 17:40:02 | | Sheet of


Motor_Ctl T i t l e | A l t i u m Li m i ted L3, 1 2 a R o d b o ro u g h R d F rench s F o res t NS W A s t r a l i a 2

Size: A4 | N umber: 6 | Rev i s i o n :


SCK D53 E1-Heater Heated-Bed E0-Heater E2-Heater THERM2 LCD_RS LCD_EN THERM3 ENC_C KILL LCD_D4 LCD_D5 LCD_D6 LCD_D7

nRESE
X-MIN Y-MIN Y-MAX Z-MIN Z-MAX

X-MIN X-MAX Y-MIN Y-MAX Z-MIN Z-MAX

X-MIN ENC_B Y-MIN Y-MAX Z-MIN Z-MAX ENC_A

X-DIR Y-EN Y-STEP Y-DIR Z-EN

2 Size: | A4 | N umber: 7 | Rev i s i o n : *


Low_MO S T i t l e | A l t i u m Li m i ted L3, 1 2 a R o d b o ro u g h R d F rench s F o res t NS W A s t r a l i a 2

Size: A4 | N umber: 8 | Rev i s i o n :

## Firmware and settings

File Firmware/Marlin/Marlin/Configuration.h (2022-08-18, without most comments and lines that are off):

#pragma once
#define CONFIGURATION_H_VERSION 02010100
#define STRING_CONFIG_H_AUTHOR "(none, default config)" // Who made the changes.
#define SHOW_BOOTSCREEN
  #define MOTHERBOARD BOARD_FYSETC_F6_14
#define SERIAL_PORT 0
#define BAUDRATE 115200
#define X_DRIVER_TYPE  TMC2209
#define Y_DRIVER_TYPE  TMC2209
#define Z_DRIVER_TYPE  TMC2209
#define E0_DRIVER_TYPE TMC2209
#define EXTRUDERS 1
#define DEFAULT_NOMINAL_FILAMENT_DIA 1.75
#define TEMP_SENSOR_0 1
#define TEMP_SENSOR_1 0
#define TEMP_SENSOR_2 0
#define TEMP_SENSOR_3 0
#define TEMP_SENSOR_4 0
#define TEMP_SENSOR_5 0
#define TEMP_SENSOR_6 0
#define TEMP_SENSOR_7 0
#define TEMP_SENSOR_BED 1
#define TEMP_SENSOR_PROBE 0
#define TEMP_SENSOR_CHAMBER 0
#define TEMP_SENSOR_COOLER 0
#define TEMP_SENSOR_BOARD 0
#define TEMP_SENSOR_REDUNDANT 0
#define DUMMY_THERMISTOR_998_VALUE  25
#define DUMMY_THERMISTOR_999_VALUE 100
#if TEMP_SENSOR_IS_MAX_TC(0)
  #define MAX31865_SENSOR_OHMS_0      100 // (Ω) Typically 100 or 1000 (PT100 or PT1000)
  #define MAX31865_CALIBRATION_OHMS_0 430 // (Ω) Typically 430 for Adafruit PT100; 4300 for Adafruit PT1000
#endif
#if TEMP_SENSOR_IS_MAX_TC(1)
  #define MAX31865_SENSOR_OHMS_1      100
  #define MAX31865_CALIBRATION_OHMS_1 430
#endif
#if HAS_E_TEMP_SENSOR
  #define TEMP_RESIDENCY_TIME         10  // (seconds) Time to wait for hotend to "settle" in M109
  #define TEMP_WINDOW                  1  // (°C) Temperature proximity for the "temperature reached" timer
  #define TEMP_HYSTERESIS              3  // (°C) Temperature proximity considered "close enough" to the target
#endif
#if TEMP_SENSOR_BED
  #define TEMP_BED_RESIDENCY_TIME     10  // (seconds) Time to wait for bed to "settle" in M190
  #define TEMP_BED_WINDOW              1  // (°C) Temperature proximity for the "temperature reached" timer
  #define TEMP_BED_HYSTERESIS          3  // (°C) Temperature proximity considered "close enough" to the target
#endif
#if TEMP_SENSOR_CHAMBER
  #define TEMP_CHAMBER_RESIDENCY_TIME 10  // (seconds) Time to wait for chamber to "settle" in M191
  #define TEMP_CHAMBER_WINDOW          1  // (°C) Temperature proximity for the "temperature reached" timer
  #define TEMP_CHAMBER_HYSTERESIS      3  // (°C) Temperature proximity considered "close enough" to the target
#endif
#if TEMP_SENSOR_REDUNDANT
  #define TEMP_SENSOR_REDUNDANT_SOURCE    E1  // The sensor that will provide the redundant reading.
  #define TEMP_SENSOR_REDUNDANT_TARGET    E0  // The sensor that we are providing a redundant reading for.
  #define TEMP_SENSOR_REDUNDANT_MAX_DIFF  10  // (°C) Temperature difference that will trigger a print abort.
#endif
#define HEATER_0_MINTEMP   5
#define HEATER_1_MINTEMP   5
#define HEATER_2_MINTEMP   5
#define HEATER_3_MINTEMP   5
#define HEATER_4_MINTEMP   5
#define HEATER_5_MINTEMP   5
#define HEATER_6_MINTEMP   5
#define HEATER_7_MINTEMP   5
#define BED_MINTEMP        5
#define CHAMBER_MINTEMP    5
#define HEATER_0_MAXTEMP 275
#define HEATER_1_MAXTEMP 275
#define HEATER_2_MAXTEMP 275
#define HEATER_3_MAXTEMP 275
#define HEATER_4_MAXTEMP 275
#define HEATER_5_MAXTEMP 275
#define HEATER_6_MAXTEMP 275
#define HEATER_7_MAXTEMP 275
#define BED_MAXTEMP      150
#define CHAMBER_MAXTEMP  60
#define HOTEND_OVERSHOOT 15   // (°C) Forbid temperatures over MAXTEMP - OVERSHOOT
#define BED_OVERSHOOT    10   // (°C) Forbid temperatures over MAXTEMP - OVERSHOOT
#define COOLER_OVERSHOOT  2   // (°C) Forbid temperatures closer than OVERSHOOT
#define PIDTEMP          // See the PID Tuning Guide at https://reprap.org/wiki/PID_Tuning
#define BANG_MAX 255     // Limits current to nozzle while in bang-bang mode; 255=full current
#define PID_MAX BANG_MAX // Limits current to nozzle while PID is active (see PID_FUNCTIONAL_RANGE below); 255=full current
#define PID_K1 0.95      // Smoothing factor within any PID loop
    #define DEFAULT_Kp  22.20
    #define DEFAULT_Ki   1.08
    #define DEFAULT_Kd 114.00
#define MAX_BED_POWER 255 // limits duty cycle to bed; 255=full current
#define MAX_CHAMBER_POWER 255 // limits duty cycle to chamber heater; 255=full current
  #define PID_FUNCTIONAL_RANGE 10 // If the temperature difference between the target temperature and the actual temperature
#define PREVENT_COLD_EXTRUSION
#define EXTRUDE_MINTEMP 170
#define PREVENT_LENGTHY_EXTRUDE
#define EXTRUDE_MAXLENGTH 200
#define THERMAL_PROTECTION_HOTENDS // Enable thermal protection for all extruders
#define THERMAL_PROTECTION_BED     // Enable thermal protection for the heated bed
#define THERMAL_PROTECTION_CHAMBER // Enable thermal protection for the heated chamber
#define THERMAL_PROTECTION_COOLER  // Enable thermal protection for the laser cooling
#define USE_XMIN_PLUG
#define USE_YMIN_PLUG
#define USE_ZMIN_PLUG
#define ENDSTOPPULLUPS
#define X_MIN_ENDSTOP_INVERTING false // Set to true to invert the logic of the endstop.
#define Y_MIN_ENDSTOP_INVERTING false // Set to true to invert the logic of the endstop.
#define Z_MIN_ENDSTOP_INVERTING false // Set to true to invert the logic of the endstop.
#define I_MIN_ENDSTOP_INVERTING false // Set to true to invert the logic of the endstop.
#define J_MIN_ENDSTOP_INVERTING false // Set to true to invert the logic of the endstop.
#define K_MIN_ENDSTOP_INVERTING false // Set to true to invert the logic of the endstop.
#define U_MIN_ENDSTOP_INVERTING false // Set to true to invert the logic of the endstop.
#define V_MIN_ENDSTOP_INVERTING false // Set to true to invert the logic of the endstop.
#define W_MIN_ENDSTOP_INVERTING false // Set to true to invert the logic of the endstop.
#define X_MAX_ENDSTOP_INVERTING false // Set to true to invert the logic of the endstop.
#define Y_MAX_ENDSTOP_INVERTING false // Set to true to invert the logic of the endstop.
#define Z_MAX_ENDSTOP_INVERTING false // Set to true to invert the logic of the endstop.
#define I_MAX_ENDSTOP_INVERTING false // Set to true to invert the logic of the endstop.
#define J_MAX_ENDSTOP_INVERTING false // Set to true to invert the logic of the endstop.
#define K_MAX_ENDSTOP_INVERTING false // Set to true to invert the logic of the endstop.
#define U_MAX_ENDSTOP_INVERTING false // Set to true to invert the logic of the endstop.
#define V_MAX_ENDSTOP_INVERTING false // Set to true to invert the logic of the endstop.
#define W_MAX_ENDSTOP_INVERTING false // Set to true to invert the logic of the endstop.
#define Z_MIN_PROBE_ENDSTOP_INVERTING false // Set to true to invert the logic of the probe.
#define DEFAULT_AXIS_STEPS_PER_UNIT   { 80, 80, 400, 500 }
#define DEFAULT_MAX_FEEDRATE          { 300, 300, 5, 25 }
#define DEFAULT_MAX_ACCELERATION      { 3000, 3000, 100, 10000 }
#define DEFAULT_ACCELERATION          3000    // X, Y, Z and E acceleration for printing moves
#define DEFAULT_RETRACT_ACCELERATION  3000    // E acceleration for retracts
#define DEFAULT_TRAVEL_ACCELERATION   3000    // X, Y, Z acceleration for travel (non printing) moves
#define DEFAULT_EJERK    5.0  // May be used by Linear Advance
  #define JUNCTION_DEVIATION_MM 0.013 // (mm) Distance from real junction edge
  #define JD_HANDLE_SMALL_SEGMENTS    // Use curvature estimation instead of just the junction angle
#define Z_MIN_PROBE_USES_Z_MIN_ENDSTOP_PIN
#define NOZZLE_TO_PROBE_OFFSET { 10, 10, 0 }
#define PROBING_MARGIN 10
#define XY_PROBE_FEEDRATE (133*60)
#define Z_PROBE_FEEDRATE_FAST (4*60)
#define Z_PROBE_FEEDRATE_SLOW (Z_PROBE_FEEDRATE_FAST / 2)
#define Z_CLEARANCE_DEPLOY_PROBE   10 // Z Clearance for Deploy/Stow
#define Z_CLEARANCE_BETWEEN_PROBES  5 // Z Clearance between probe points
#define Z_CLEARANCE_MULTI_PROBE     5 // Z Clearance between multiple probes
#define Z_PROBE_LOW_POINT          -2 // Farthest distance below the trigger-point to go before stopping
#define Z_PROBE_OFFSET_RANGE_MIN -20
#define Z_PROBE_OFFSET_RANGE_MAX 20
#define X_ENABLE_ON 0
#define Y_ENABLE_ON 0
#define Z_ENABLE_ON 0
#define E_ENABLE_ON 0 // For all extruders
#define DISABLE_X false
#define DISABLE_Y false
#define DISABLE_Z false
#define DISABLE_E false             // Disable the extruder when not stepping
#define DISABLE_INACTIVE_EXTRUDER   // Keep only the active extruder enabled
#define INVERT_X_DIR false
#define INVERT_Y_DIR true
#define INVERT_Z_DIR false
#define INVERT_E0_DIR false
#define INVERT_E1_DIR false
#define INVERT_E2_DIR false
#define INVERT_E3_DIR false
#define INVERT_E4_DIR false
#define INVERT_E5_DIR false
#define INVERT_E6_DIR false
#define INVERT_E7_DIR false
#define X_HOME_DIR -1
#define Y_HOME_DIR -1
#define Z_HOME_DIR -1
#define X_BED_SIZE 200
#define Y_BED_SIZE 200
#define X_MIN_POS 0
#define Y_MIN_POS 0
#define Z_MIN_POS 0
#define X_MAX_POS X_BED_SIZE
#define Y_MAX_POS Y_BED_SIZE
#define Z_MAX_POS 200
#define MIN_SOFTWARE_ENDSTOPS
  #define MIN_SOFTWARE_ENDSTOP_X
  #define MIN_SOFTWARE_ENDSTOP_Y
  #define MIN_SOFTWARE_ENDSTOP_Z
  #define MIN_SOFTWARE_ENDSTOP_I
  #define MIN_SOFTWARE_ENDSTOP_J
  #define MIN_SOFTWARE_ENDSTOP_K
  #define MIN_SOFTWARE_ENDSTOP_U
  #define MIN_SOFTWARE_ENDSTOP_V
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

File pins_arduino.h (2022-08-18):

/*
  pins_arduino.h - Pin definition functions for Arduino
  Part of Arduino - http://www.arduino.cc/

  Copyright (c) 2007 David A. Mellis

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
  You should have received a copy of the GNU Lesser General
  Public License along with this library; if not, write to the
  Free Software Foundation, Inc., 59 Temple Place, Suite 330,
  Boston, MA  02111-1307  USA
*/

#ifndef Pins_Arduino_h
#define Pins_Arduino_h

#include <avr/pgmspace.h>

#define NUM_DIGITAL_PINS            85
#define NUM_ANALOG_INPUTS           16
#define analogInputToDigitalPin(p)  ((p < 16) ? (p) + 54 : -1)
#define digitalPinHasPWM(p)         (((p) >= 2 && (p) <= 13) || ((p) >= 44 && (p)<= 46))

#define PIN_SPI_SS    (53)
#define PIN_SPI_MOSI  (51)
#define PIN_SPI_MISO  (50)
#define PIN_SPI_SCK   (52)

static const uint8_t SS   = PIN_SPI_SS;
static const uint8_t MOSI = PIN_SPI_MOSI;
static const uint8_t MISO = PIN_SPI_MISO;
static const uint8_t SCK  = PIN_SPI_SCK;

#define PIN_WIRE_SDA        (20)
#define PIN_WIRE_SCL        (21)

static const uint8_t SDA = PIN_WIRE_SDA;
static const uint8_t SCL = PIN_WIRE_SCL;

#define LED_BUILTIN 13

#define PIN_A0   (54)
#define PIN_A1   (55)
#define PIN_A2   (56)
#define PIN_A3   (57)
#define PIN_A4   (58)
#define PIN_A5   (59)
#define PIN_A6   (60)
#define PIN_A7   (61)
#define PIN_A8   (62)
#define PIN_A9   (63)
#define PIN_A10  (64)
#define PIN_A11  (65)
#define PIN_A12  (66)
#define PIN_A13  (67)
#define PIN_A14  (68)
#define PIN_A15  (69)

static const uint8_t A0 = PIN_A0;
static const uint8_t A1 = PIN_A1;
static const uint8_t A2 = PIN_A2;
static const uint8_t A3 = PIN_A3;
static const uint8_t A4 = PIN_A4;
static const uint8_t A5 = PIN_A5;
static const uint8_t A6 = PIN_A6;
static const uint8_t A7 = PIN_A7;
static const uint8_t A8 = PIN_A8;
static const uint8_t A9 = PIN_A9;
static const uint8_t A10 = PIN_A10;
static const uint8_t A11 = PIN_A11;
static const uint8_t A12 = PIN_A12;
static const uint8_t A13 = PIN_A13;
static const uint8_t A14 = PIN_A14;
static const uint8_t A15 = PIN_A15;

// A majority of the pins are NOT PCINTs, SO BE WARNED (i.e. you cannot use them as receive pins)
// Only pins available for RECEIVE (TRANSMIT can be on any pin):
// (I've deliberately left out pin mapping to the Hardware USARTs - seems senseless to me)
// Pins: 10, 11, 12, 13,  50, 51, 52, 53,  62, 63, 64, 65, 66, 67, 68, 69 ,73							  
#define digitalPinToPCICR(p)    ( (((p) >= 10) && ((p) <= 13)) || \
                                  (((p) >= 50) && ((p) <= 53)) || \
                                  (((p) >= 62) && ((p) <= 69)) || \
								  (((p) == 72) || ((p) == 73)) || \
								  (((p) == 75) || ((p) == 76)) || \
								  ((p) == 77) ? (&PCICR) : ((uint8_t *)0) )

#define digitalPinToPCICRbit(p) ( (((p) >= 10) && ((p) <= 13)) || (((p) >= 50) && ((p) <= 53)) ? 0 : \
                                ( (((p) >= 62) && ((p) <= 69)) ? 2 : \
                                ( (((p) >= 72) && ((p) <= 77)) ? 1:0 )))

#define digitalPinToPCMSK(p)    ( (((p) >= 10) && ((p) <= 13)) || (((p) >= 50) && ((p) <= 53)) ? (&PCMSK0) : \
                                ( (((p) >= 62) && ((p) <= 69)) ? (&PCMSK2) : \
                                ( (((p) >= 72) && ((p) <= 77)) ? (&PCMSK1):((uint8_t *)0) ) ) )

#define digitalPinToPCMSKbit(p) ( (((p) >= 10) && ((p) <= 13)) ? ((p) - 6) : \
                                ( ((p) == 50) ? 3 : \
                                ( ((p) == 51) ? 2 : \
                                ( ((p) == 52) ? 1 : \
                                ( ((p) == 53) ? 0 : \
                                ( (((p) >= 62) && ((p) <= 69)) ? ((p) - 62) : \
								( (((p) >= 72) && ((p) <= 73)) ? ((p) - 69) : \
								( (((p) >= 75) && ((p) <= 77)) ? ((p) - 70) : \
                                0 ) ) ) ) ) ) ) )

#define digitalPinToInterrupt(p) ((p) == 2 ? 0 : ((p) == 3 ? 1 : ((p) >= 18 && (p) <= 21 ? 23 - (p) : NOT_AN_INTERRUPT)))

#ifdef ARDUINO_MAIN

const uint16_t PROGMEM port_to_mode_PGM[] = {
	NOT_A_PORT,
	(uint16_t) &DDRA,
	(uint16_t) &DDRB,
	(uint16_t) &DDRC,
	(uint16_t) &DDRD,
	(uint16_t) &DDRE,
	(uint16_t) &DDRF,
	(uint16_t) &DDRG,
	(uint16_t) &DDRH,
	NOT_A_PORT,
	(uint16_t) &DDRJ,
	(uint16_t) &DDRK,
	(uint16_t) &DDRL,
};

const uint16_t PROGMEM port_to_output_PGM[] = {
	NOT_A_PORT,
	(uint16_t) &PORTA,
	(uint16_t) &PORTB,
	(uint16_t) &PORTC,
	(uint16_t) &PORTD,
	(uint16_t) &PORTE,
	(uint16_t) &PORTF,
	(uint16_t) &PORTG,
	(uint16_t) &PORTH,
	NOT_A_PORT,
	(uint16_t) &PORTJ,
	(uint16_t) &PORTK,
	(uint16_t) &PORTL,
};

const uint16_t PROGMEM port_to_input_PGM[] = {
	NOT_A_PIN,
	(uint16_t) &PINA,
	(uint16_t) &PINB,
	(uint16_t) &PINC,
	(uint16_t) &PIND,
	(uint16_t) &PINE,
	(uint16_t) &PINF,
	(uint16_t) &PING,
	(uint16_t) &PINH,
	NOT_A_PIN,
	(uint16_t) &PINJ,
	(uint16_t) &PINK,
	(uint16_t) &PINL,
};
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

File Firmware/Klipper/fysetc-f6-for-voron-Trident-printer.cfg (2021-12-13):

# This file contains common pin mappings for a Fysetc F6 board.
# To use this config, the firmware should be compiled for the AVR atmega2560.

# See docs/Config_Reference.md for a description of parameters.


## Thermistor Types
##   "EPCOS 100K B57560G104F"
##   "ATC Semitec 104GT-2"
##   "NTC 100K beta 3950"
##   "Honeywell 100K 135-104LAG-J01"
##   "NTC 100K MGB18-104F39050L32"
##   "AD595"
##   "PT100 INA826"
##===================================================================.

[virtual_sdcard]
path: ~/gcode_files

[pause_resume]
[display_status]

[mcu]
###Change to device found by "ls -l /dev/serial/by-id/" with just one this MCU connected to Pi
serial: /dev/serial/by-id/usb-1a86_USB2.0-Serial-if00-port0

[printer]
kinematics: corexy
max_velocity: 300
max_accel: 5000
max_z_velocity: 5
max_z_accel: 100
square_corner_velocity: 5.0  

#####################################################################
# 	X/Y Stepper Settings
#####################################################################\

######
#X motor slot on main board (B Motor)
###############
[stepper_x]
step_pin: PF0
dir_pin: PF1
enable_pin: !PD7
microsteps: 16
rotation_distance: 40
full_steps_per_rotation: 400
endstop_pin: PK1  # PK2 for X-max
position_min: 0
##	Uncomment below for 250mm build
position_endstop: 250
position_max: 250

##	Uncomment for 300mm build
#position_endstop: 300
#position_max: 300

##	Uncomment for 350mm build
#position_endstop: 350
#position_max: 350

##--------------------------------------------------------------------
homing_speed: 25   #Max 100
homing_retract_dist: 5
homing_positive_dir: true

[tmc2209 stepper_x]
uart_pin: PG3
run_current: 0.900
hold_current: 0.750
#stealthchop_threshold: 250

######
#Y motor slot on main board (A Motor)
###############
[stepper_y]
step_pin: PF6
dir_pin: PF7
enable_pin: !PF2
microsteps: 16
rotation_distance: 40
full_steps_per_rotation: 400
endstop_pin: PJ1  # PJ0 for Y-max
##--------------------------------------------------------------------
##	Uncomment for 250mm build
position_endstop: 250
position_max: 250

##	Uncomment for 300mm build
#position_endstop: 300
#position_max: 300

##	Uncomment for 350mm build
#position_endstop: 350
#position_max: 350
##--------------------------------------------------------------------
homing_speed: 25  #Max 100
homing_retract_dist: 5
homing_positive_dir: true

[tmc2209 stepper_y]
uart_pin: PJ3
run_current: 0.900
hold_current: 0.750


#####################################################################
# 	Z Stepper Settings
#####################################################################

######
# Z0 Stepper - Left Front
# M1 motor slot on expander board 
###############
[stepper_z]
step_pin: PL6
dir_pin: PL1
enable_pin: !PF4
microsteps: 16
##T8x4 Lead Screws.  One rotation moves the bed 4mm 
##Change according to integrated steppers purchased
rotation_distance: 4
full_steps_per_rotation: 200
endstop_pin: PB6  # PE4 for Z-max
#  Z-position of nozzle (in mm) to z-endstop trigger point relative to print surface (Z0)
#  (+) value = endstop above Z0, (-) value = endstop below
#  Increasing position_endstop brings nozzle closer to the bed
#  After you run Z_ENDSTOP_CALIBRATE, position_endstop will be stored at the very end of your config
position_endstop: -0.5
## All builds use same Max Z
position_max: 250
position_max: 250
position_min: -2.5
homing_speed: 35.0

[tmc2209 stepper_z]
uart_pin: PE2
run_current: 0.650
hold_current: 0.450
stealthchop_threshold: 30

######
#M2 motor slot on expander board (Rear Z)
###############
[stepper_z1]
step_pin: PA4
dir_pin: !PA6
enable_pin: !PA2
microsteps: 16
rotation_distance: 4
full_steps_per_rotation: 200

[tmc2209 stepper_z1]
uart_pin: PJ5
run_current: 0.650
hold_current: 0.450
stealthchop_threshold: 30

######
#M3 motor slot on expander board (Right Front Z)
###############
[stepper_z2]
step_pin: PC1
dir_pin: !PC3
enable_pin: !PC7
microsteps: 16
rotation_distance: 4
full_steps_per_rotation: 200

[tmc2209 stepper_z2]
uart_pin: PE7
run_current: 0.650
hold_current: 0.450
stealthchop_threshold: 30



######
#E0 motor slot on main board
###############
[extruder]
max_extrude_cross_section: 50
max_extrude_only_distance: 700.00
step_pin: PF5
dir_pin: !PF3
enable_pin: !PG1
microsteps: 16
# Tune per individual printer
# Default for Bondtech 5mm Bore Drive Gears
rotation_distance: 22.6789511
full_steps_per_rotation: 200
gear_ratio: 50:17
nozzle_diameter: 0.400
filament_diameter: 1.750
pressure_advance: 0.67
pressure_advance_smooth_time: 0.040
heater_pin: PE3
##	Validate the following thermistor type to make sure it is correct
sensor_type: NTC 100K beta 3950
sensor_pin: PK4
min_extrude_temp: 180
min_temp: 0
max_temp: 300
control = pid
pid_kp = 26.213
pid_ki = 1.304
pid_kd = 131.721
#Set appropriate once tuning your printer
#pressure_advance: .05
##	Default is 0.040, leave stock
pressure_advance_smooth_time: 0.040

[tmc2209 extruder]
uart_pin: PA1
run_current: 0.5
hold_current: 0.4
sense_resistor: 0.110
stealthchop_threshold: 0

#####################################################################
# 	Bed Heater
#####################################################################   
[heater_bed]
heater_pin: PH5
##  Choose the correct thermistor for your heater
sensor_type: EPCOS 100K B57560G104F
sensor_pin: PK7
##	Adjust Max Power so your heater doesn't warp your bed
max_power: 0.6
min_temp: 0
max_temp: 120
control: pid
pid_kp: 58.437
pid_ki: 2.347
pid_kd: 363.769

#####################################################################
# 	Probe
#####################################################################

######
#Z Max Connector on Z(main) Board
#Inductive Probe
#This probe is not used for Z height, only Z Tilt Adjust
###############
[probe]
pin: PE4
x_offset: 0
y_offset: 25.0
z_offset: 0
speed: 10.0
samples: 1
samples_result: average
sample_retract_dist: 2.0
samples_tolerance: 0.05
samples_tolerance_retries: 3

#####################################################################
# 	Fan Control
#####################################################################

######
#Part Cooling Fan
#HE1 Connector on Main Board
###############
[fan]
pin: PL5

######
#Hotend Cooling Fan
#Fan0 Connector on Main Board
###############
[heater_fan hotend_fan]
pin: PL4
max_power: 1.0
kick_start_time: 0.5
heater: extruder
heater_temp: 50.0

## Any additional fans can be driven by Fan1/Fan3 slots
## at full power on the main board, or alternative solutions
## may be sought for MOSFET controlled ports.

#####################################################################
# 	Homing and Gantry Adjustment Routines
#####################################################################

[idle_timeout]
timeout: 1800

[homing_override]
axes: z
set_position_z: 0
gcode:
   G90
   G0 Z5 F600
   G28 X Y
   ##	XY Location of the Z Endstop Switch
   ##	Update X and Y to your values (such as X157, Y305) after going through
   ##	Z Endstop Pin Location Definition step.
   G0 X-10 Y-10 F3600 
   
   G28 Z
   G0 Z10 F1800

      
   	##	Uncomment for for your size printer:
   	## 	Rough measurement is the middle of your bed.
#--------------------------------------------------------------------
   	##	Uncomment for 250mm build
   	G0 X125 Y125 Z30 F3600
   
	##	Uncomment for 300 build
   	#G0 X150 Y150 Z30 F3600

    ##	Uncomment for 350 build
   	#G0 X175 Y175 Z30 F3600
#--------------------------------------------------------------------

#####################################################################
# 	Displays
#####################################################################

#Using the EXP-MOT Expander uses up standard Mini FYSETC Capable Display
#Ports.  Other solutions must be procured.

#####################################################################
# 	Macros
#####################################################################

[z_tilt]
##	Use Z_TILT_ADJUST to level the bed .
##	z_positions: Location of toolhead

##--------------------------------------------------------------------
## Uncomment below for 250mm build
z_positions:
	-50, 18
	125, 298
	300, 18
points:
	30, 5
	125, 195
	220, 5

## Uncomment below for 300mm build
#z_positions:
#	-50, 18
#	150, 348
#	350, 18

#points:
#	30, 5
#	150, 245
#	270, 5

## Uncomment below for 350mm build
#z_positions:
#	-50, 18
#	175, 398
#	400, 18
#points:
#	30, 5
#	175, 295
#	320, 5


##--------------------------------------------------------------------

speed: 200
horizontal_move_z: 10
retries: 5
retry_tolerance: 0.0075
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

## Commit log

2018-10-25 upload 2d file
    [F6 V1.3 2D.DWG]
2020-07-28 add V1.4
    [F6 V1.3 2D.DWG]
2020-11-20 Upload firmware
    [Configuration.h, Configuration_adv.h]
2020-12-08 Enable Serial 2
    [Configuration.h]
2021-12-13 Add Voron example
    [fysetc-f6-for-voron-Trident-printer.cfg, fysetc-f6-for-voron.stl]
2022-08-18 Update Marlin
    [Configuration.h, Configuration_adv.h, F6 V1.3 2D.DWG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]

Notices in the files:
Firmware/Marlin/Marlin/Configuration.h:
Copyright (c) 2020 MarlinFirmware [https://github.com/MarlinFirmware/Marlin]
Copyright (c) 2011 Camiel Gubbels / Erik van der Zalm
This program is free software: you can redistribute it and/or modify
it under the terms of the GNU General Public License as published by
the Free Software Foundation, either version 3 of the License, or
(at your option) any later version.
